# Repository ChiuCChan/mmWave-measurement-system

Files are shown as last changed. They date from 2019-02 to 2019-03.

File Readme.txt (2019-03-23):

=============Title=======================
Open-Source and Low-Cost Test Bed for Automated 5G Channel Measurement in mmWave Band

=============Movitation==================
To provide an affordable and open-source test-bed solution for mmWave channel modeling 
covering 24 GHz and 77 GHz bands. 

=============Built with Arduino==========

=============Specification==========
Carrier frequnecy	24GHz		77GHz
Signal bandwidth	15kHz		0.15MHz
Transmit power		20 +/- 1 dBm    25 +/- 2 dBm
Antenna Gain		20 dB		20 dB
H-plane beamwidth	80 deg		15 deg
E-plane beamwidth	12 deg		15 deg

=============Library used================
---24 Ghz module---
Wire.h Adafruit_MCP4725.h stdlib.h

---Base Unit---
<AccelStepper.h> <Adafruit_GFX.h> <Adafruit_SSD1306.h> <SPI.h> 
<RF24.h>(from github) <stdlib.h> <string.h> <TinyGPS++.h>

---Base Station---
<RF24.h> <SPI.h>

===========Electronics BoQ================
RS232+BT x2
Op Amp x2
Arduino nano x2
Arduino Duo x3
GY-4988 x2
nRF24L01 x2
Antenna x3 
OLED x2
ADC+DACx2
Doppler Radar RS3400 x2(77GHz)x2
Doppler Radar KLC-6 x2(24GHz) x2
GPS+RTL x2
Power regulator (YL105) x2
XY42STH34-1504A (High Stepper motor) x2

==================Pin setup================
---24 GHz module---
A0<->KLC6 Output

---Base Unit---
Serial 2 <-> GPS
Pin 50 <-> 4988 stepPin
Pin 51 <-> 4988 DirectionPin
Pin 46 <-> Optical switch Output
Pin 12 <-> OLED_CLK   
Pin 11 <-> OLED_MOSI  
Pin 10 <-> OLED_RESET 
Pin 09 <-> OLED_DC   
Pin 08 <-> OLED_CS   
Pin 13 <-> OLED_Power
Pin 52 <-> NF24L01 CEpin
Pin 53 <-> Nf24L01 CSpin

---Base Station---
Pin 52 <-> NF24L01 CEpin
Pin 53 <-> Nf24L01 CSpin

=============How to use?====================
comply different programs with respect to the corresponding unit.

For 77GHz radar measurement, RS232<->TTL modules are required for communication between Base Unit and 77GHz radar.
Or connect to the PC using RS232 and run the SiversIMA_Controller.m directly from the PC.
Run the BaseStation program and log into the Base Station CLI using arduino IDE or Putty

Using the following command to control the base unit, 77GHz, 24GHz radars.

//          Command                   Code             Respond
//          Force initialization      NNM01#          ”OK”
//          Reset angle               NNM02#          ”OK”
//          Get status                NNM03#           <text>
//          Get coordinates           NNM04#           S dd.dd / E ddd.dd
//          Get current angle         NNM05#            +/- ssss
//          relay                     NNM06<text>#      "Sent"
//          Go to angle               NNM10(+/-)ssss#   ”Go to +/- ssss”
//          Set 24GHz VCO voltage     NNM23VV#          "Set VCO to VV"
//	    Perform Sweeping from     NNM22VVVV#	Measurement data
	    VV to VV
//	    Troubleshooting	      NNM21#		Measurement data

The 77GHz radar command please refer to Sivers IMA RS3400 manual

==================Contribute==================
The Base Station and Base Unit program is programmed by Chiu Chan
The 24GHz radar controlling program is programmed by Ferdi Kurnia
The 77GHz radar controlling program is programmed by Akram Hourani

==================Credits==================
Thanks for the colleagues from RMIT University, AU for the hardware development and 3D printing 

==================License==================
Electronic & Telecommunication department, RMIT University, hereby disclaims all copyright interest in the program "mmWave measurement testbed" written by Chiu Chan, Ferdi Kurnia, Akram Hourani.

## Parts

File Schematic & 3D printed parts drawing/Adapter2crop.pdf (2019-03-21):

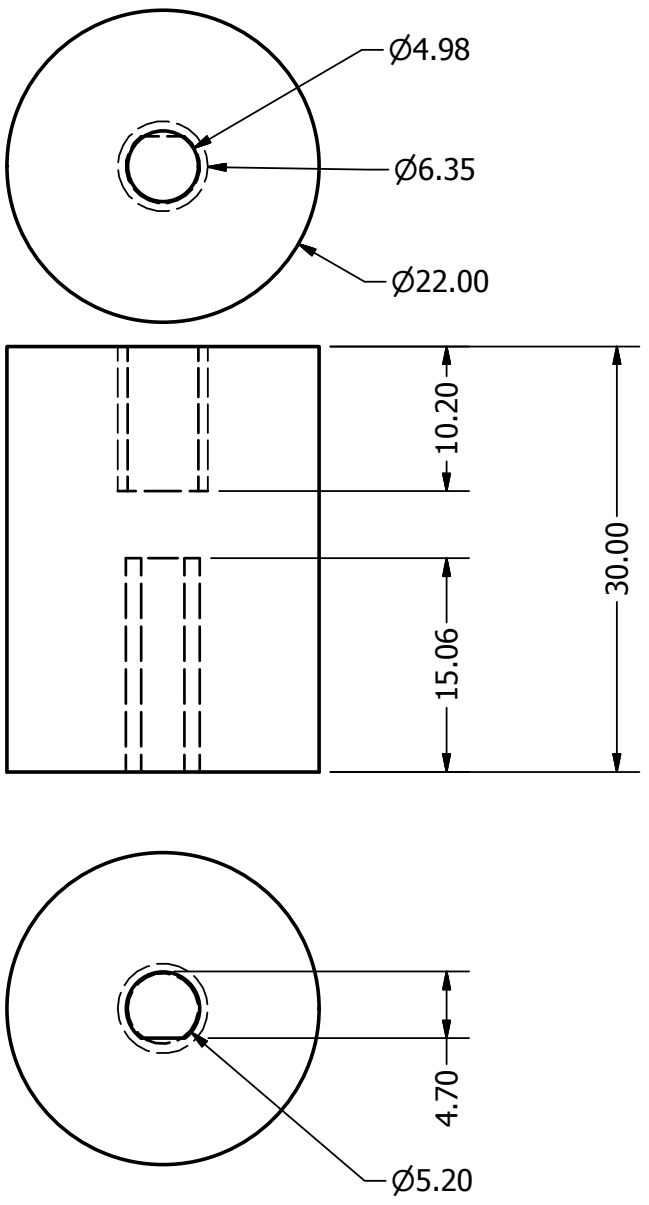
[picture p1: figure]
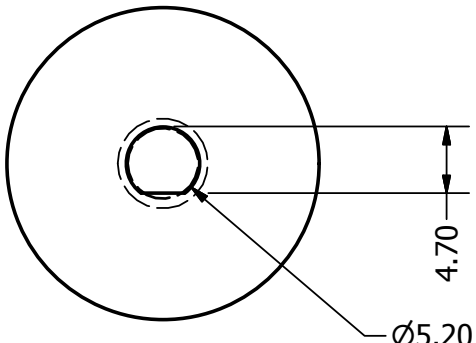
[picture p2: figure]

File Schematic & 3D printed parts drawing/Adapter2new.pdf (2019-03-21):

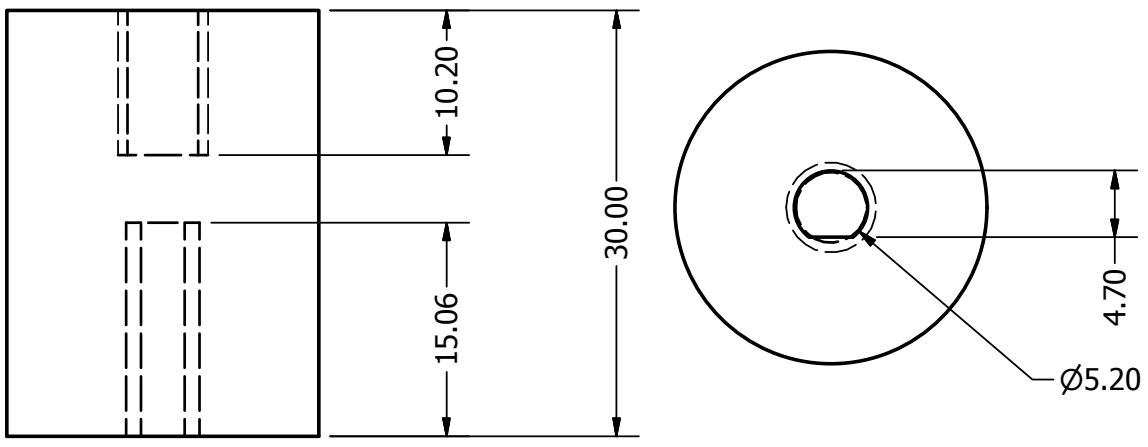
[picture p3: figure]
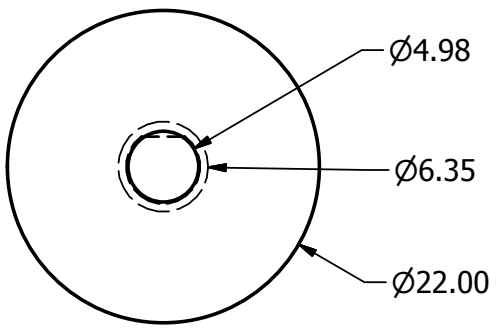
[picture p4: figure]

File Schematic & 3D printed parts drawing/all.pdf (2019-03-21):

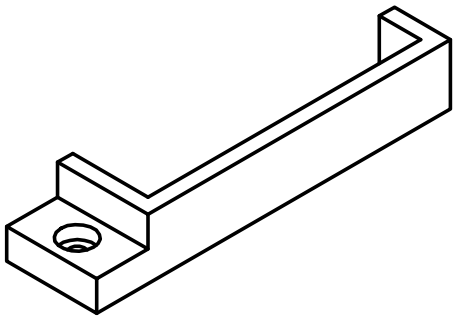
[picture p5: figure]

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
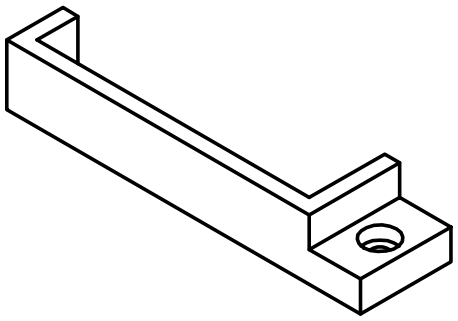
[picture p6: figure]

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
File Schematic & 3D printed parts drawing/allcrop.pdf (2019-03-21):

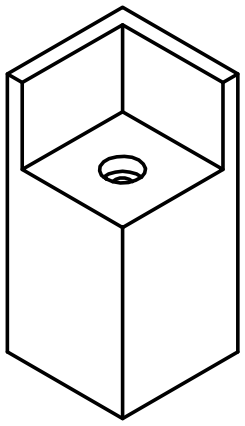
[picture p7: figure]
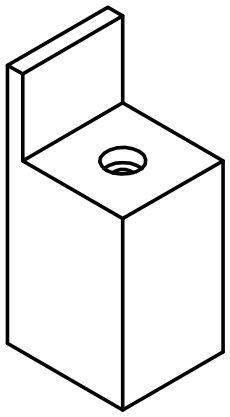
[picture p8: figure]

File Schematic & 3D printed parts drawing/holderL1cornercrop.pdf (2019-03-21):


3.00



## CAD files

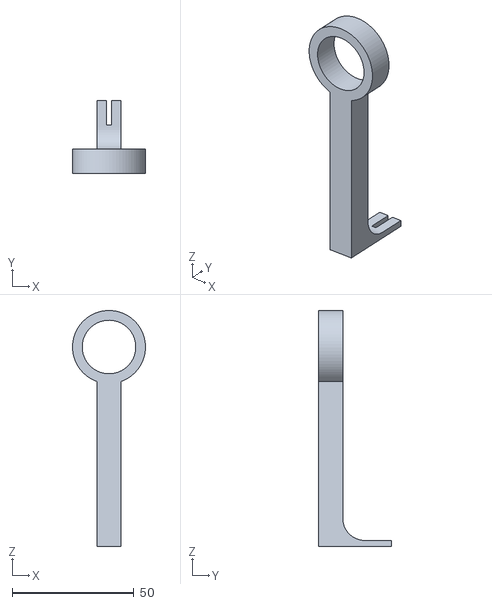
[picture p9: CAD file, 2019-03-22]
Schematic & 3D printed parts drawing/reseter-new-10.stl
30.0 x 30.0 x 97.0

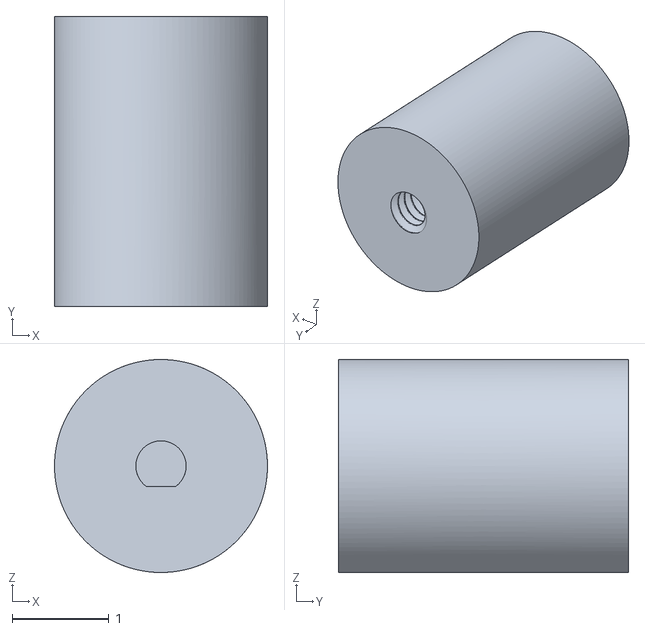
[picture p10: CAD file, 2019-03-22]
Schematic & 3D printed parts drawing/Adapter2-new.stl
2.20 x 3.00 x 2.20

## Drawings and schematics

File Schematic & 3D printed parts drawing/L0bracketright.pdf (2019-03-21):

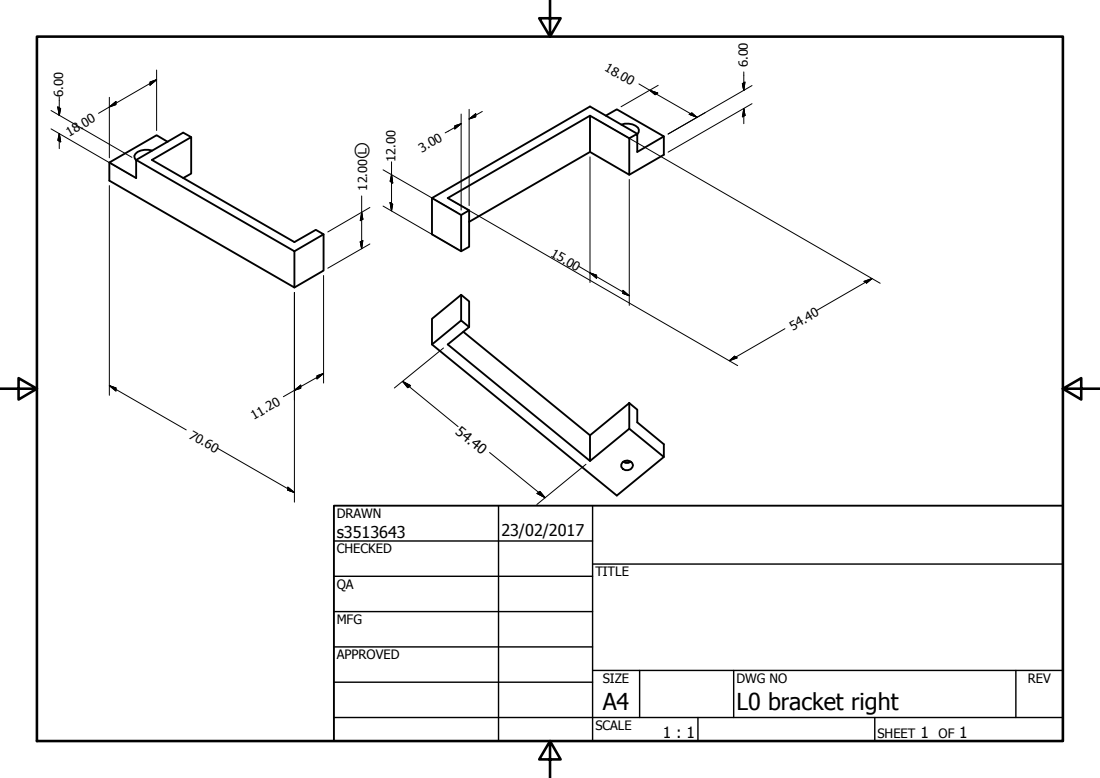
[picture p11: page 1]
SHEET 1 OF 1; DRAWN; CHECKED; MFG; APPROVED; DWG NO L0 bracket right; TITLE; SIZE A4; SCALE; REV

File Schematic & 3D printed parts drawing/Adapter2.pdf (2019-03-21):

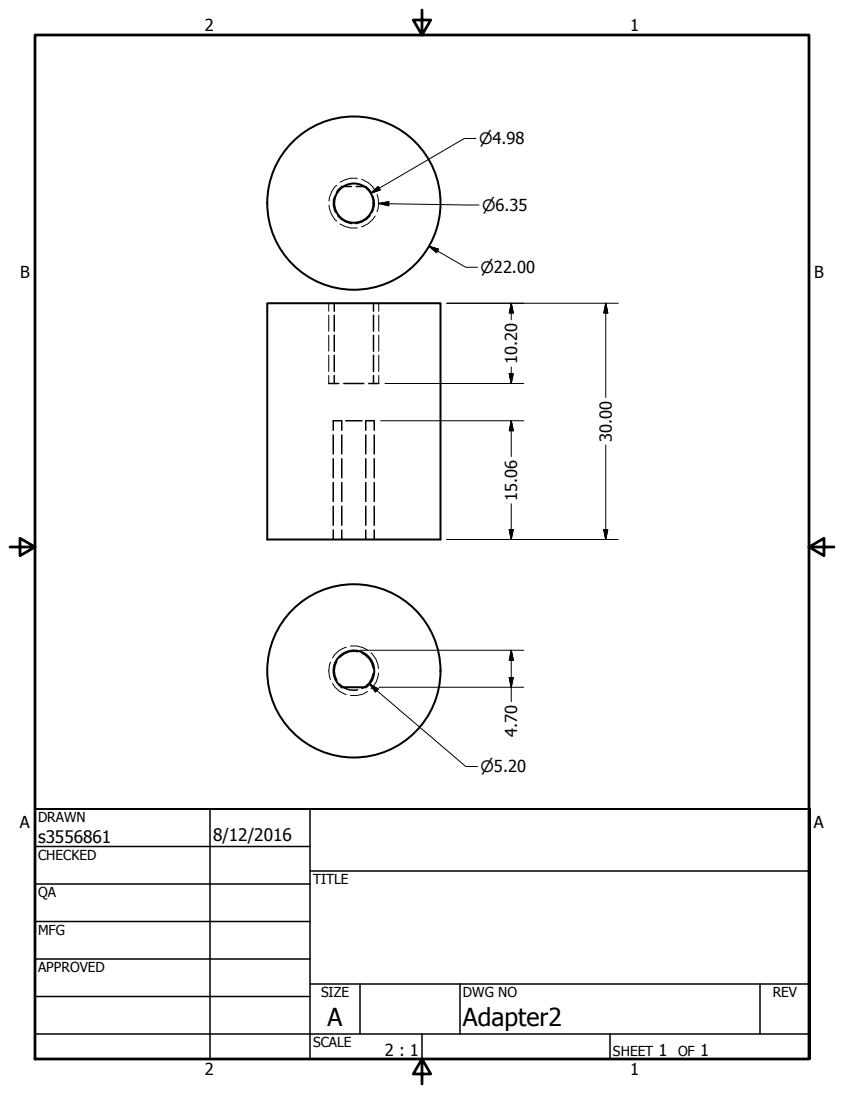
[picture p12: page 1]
SHEET 1 OF 1; DRAWN; CHECKED; MFG; APPROVED; DWG NO Adapter2; TITLE; SIZE A; SCALE; REV

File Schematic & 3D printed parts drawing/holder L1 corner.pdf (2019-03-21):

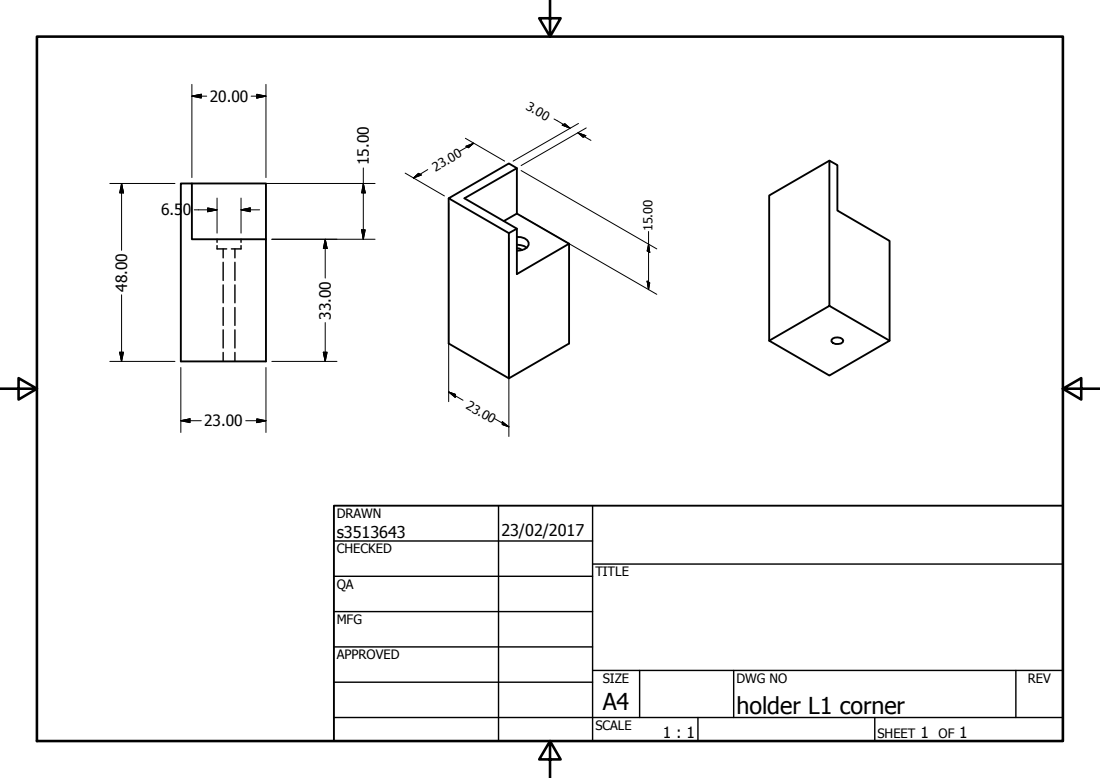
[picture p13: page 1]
SHEET 1 OF 1; DRAWN; CHECKED; MFG; APPROVED; DWG NO holder L1 corner; TITLE; SIZE A4; SCALE; REV

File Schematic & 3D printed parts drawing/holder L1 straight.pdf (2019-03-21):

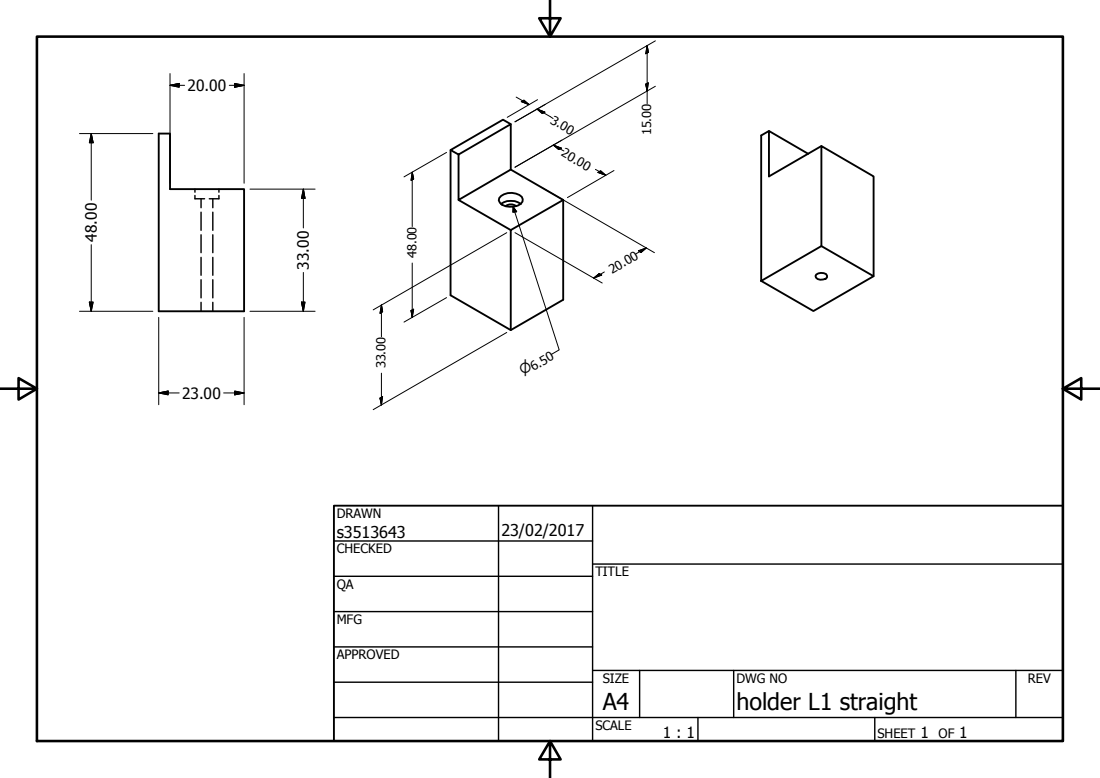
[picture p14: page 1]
SHEET 1 OF 1; DRAWN; CHECKED; MFG; APPROVED; DWG NO holder L1 straight; TITLE; SIZE A4; SCALE; REV

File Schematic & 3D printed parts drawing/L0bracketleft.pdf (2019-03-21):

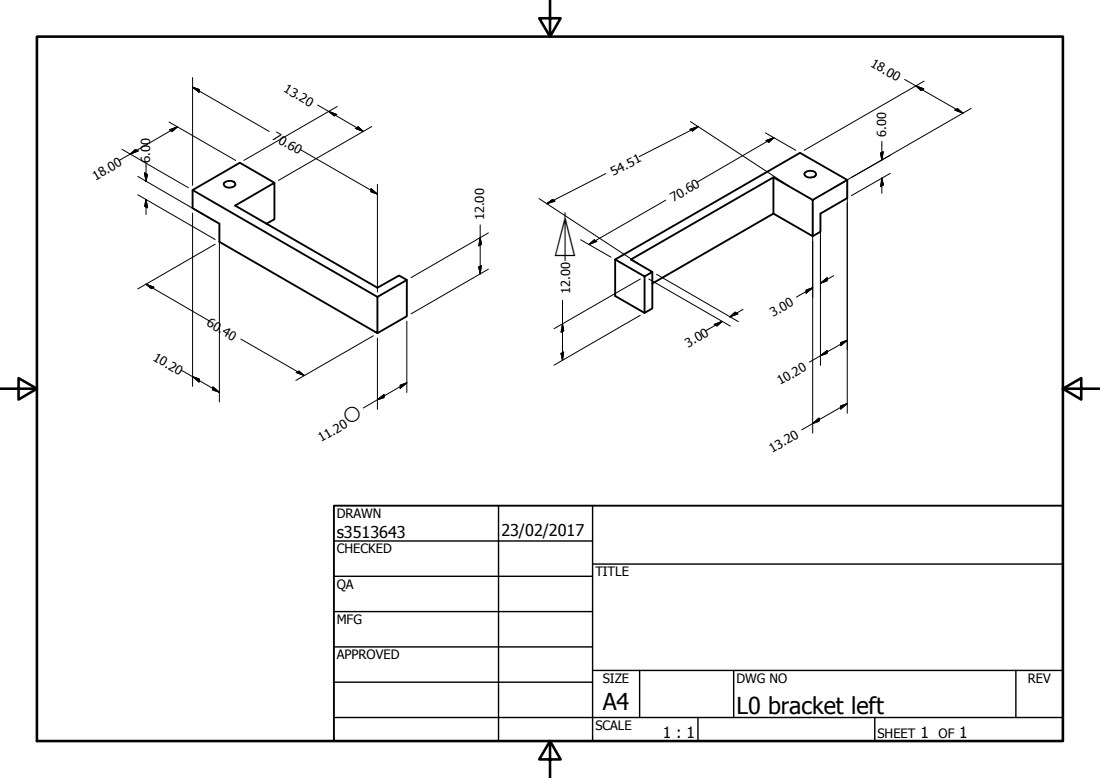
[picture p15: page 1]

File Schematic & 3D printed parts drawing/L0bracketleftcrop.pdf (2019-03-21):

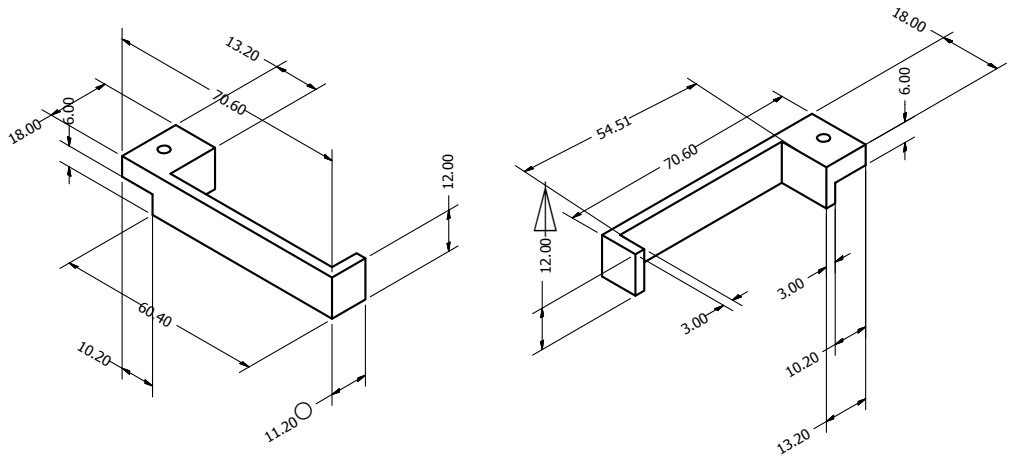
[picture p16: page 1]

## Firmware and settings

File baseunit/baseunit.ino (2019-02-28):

//
//float val = 0;          // variable to store the value read
//float Voltage;          // Analog voltage
//float Volt[10];         // Analog voltage array
//float averagevolt=0;    // average of the input voltage
//int displaycounter=0;
//#define analogPin 3     // potentiometer wiper (middle terminal) connected to analog pin 
                          // outside leads to ground and +5V


/**************************************************/
#include <AccelStepper.h>
#include <Adafruit_GFX.h>
#include <Adafruit_SSD1306.h>
#include <SPI.h>
#include "RF24.h"
#include <stdlib.h>
#include <string.h>
#include <TinyGPS++.h>
/**************************************************/
// The TinyGPS++ object
TinyGPSPlus gps;
#define ss Serial2
#define GPSBaud 9600    // GPS have to be 9600Hz 
/**************************************************/
//NEMA 17 motor pins
#define DRIVER 1
#define stepPin 50
#define dirPin 51       // initialize the stepper library on pins 50 51: 51=step 50=direction
AccelStepper myStepper(DRIVER,stepPin, dirPin);
/**************************************************/
//Optical Switch pin
#define opticalsw 46
/**************************************************/
// OLED screen pins
#define OLED_CLK   12
#define OLED_MOSI  11
#define OLED_RESET 10
#define OLED_DC    9
#define OLED_CS    8
#define OLED_Power 13
#define Buzzer 3
Adafruit_SSD1306 display(OLED_MOSI, OLED_CLK, OLED_DC, OLED_RESET, OLED_CS);
/**************************************************/
//Radio pin
#define CEpin 52
#define CSpin 53

/***********************************************************/
/***      Set this radio as radio number 0 or 1         ***/
char radiodisplay[32];
int radioNumber = 1; // 0, 1for arduino RX; 2 for MATLAB RECEIVER
byte incomingByte;     // When byte is received from the Radio
short int Buffer_index = 0;
char inData[52];       //Serial data buffer
char Command[52];      //The command received from serial port
double latdeg = 0;     //GPS latitude degree
double longdeg = 0;    //GPS longitude degree
bool error = 0;       //for checking command error
double angle=0;       //used to record current angle
String serialbuffer;
char charbuffer[1000];
char buffershort[32];
/* Hardware configuration: Set up nRF24L01 radio on SPI bus plus pins 7 & 8 */
RF24 radio(CEpin, CSpin); // (uint8_t _cepin, uint8_t _cspin)
/**********************************************************/
//byte addresses[3][6] = {"1Node", "2Node","3Node"};

byte Node1[2][7] = {"1Node", "2Node"};
byte Node2[2][7] = {"3Node", "4Node"};

// Used to control whether this node is sending or receiving

// Our function
void beep(unsigned char delayms) 
 { //creating function
  digitalWrite(Buzzer, LOW); //Setting pin to low
  delay(delayms); //Delaying
  digitalWrite(Buzzer ,HIGH); //Setting pin to high
  delay(delayms); //Delaying;r
 }
 
void moveto()
{
 char Stepc[4];
 int Stepint = 0;

 memset(Stepc,0,sizeof(Stepc));
              for (int i = 0 ; i < 4; i++) 
              {
                Stepc[i] = Command[i + 7]; //copy  digits 7,8,9,10 step
              }
              if (strstr(Command,"+"))
              {
              //  display.println("debug1");
                Stepint=atoi(Stepc);
              }
              else if (strstr(Command,"-"))
              {
                //display.println("debug2");
                Stepint= -atoi(Stepc);
              }
              display.print("Move to position");
              display.println(Stepint); 
              Serial.println(Stepc);
              display.display();
              radio.write("N2 moved to position:",21);
              radio.write(Stepc,sizeof(Stepc));
              radio.write("\r",2);
              myStepper.setCurrentPosition(0);      
              myStepper.runToNewPosition(Stepint); // Move steps (1.8 degree for one step)
              angle+=(Stepint*1.8)/16;
              angle=angle/360;
         
              delay(2000);
}

void getstatus(double currentangle)
{
  radio.write("Current Angle:\r",15);
  memset(radiodisplay,0,32);
  snprintf(radiodisplay,32,"%f",currentangle);
  radio.write(&radiodisplay, sizeof(radiodisplay));
  radio.write("\r",2);
}
void relay()
{
  char msg32[32];
  memset(msg32,0,sizeof(msg32));
  for(int i=0; Command[i + 6] != '#' ;i++)
  {
    msg32[i] = Command[i + 6]; //copy  digits 6,8,9,10 step
  }
  
  serialbuffer =String(msg32);
  
  Serial1.print(serialbuffer + "\r");
  Serial.println(serialbuffer);        //for debug
  display.println(serialbuffer);
  display.display();
  delay(100);
}


void relay22()
{
  char msg32[32];
  memset(msg32,0,sizeof(msg32));
  int i=0;
  for(i=0; Command[i + 6] != '#' ;i++)
  {
    msg32[i] = Command[i + 6]; //copy  digits 6,8,9,10 step
  }
  msg32[i] = '#';
  serialbuffer =String(msg32);
  
  Serial3.print(serialbuffer);
  Serial.println(serialbuffer);        //for debug
  display.println(serialbuffer);
  display.display();
  //delay(100);
}

void calibrate()
{
  radio.write("Start Calibrate\r",17);
  for(int i=0;i<360;i++)
  {
      myStepper.setCurrentPosition(0);      
      myStepper.runToNewPosition(8.888); // Move one step (1.8 degree for one step)
      if (digitalRead(opticalsw) == LOW)       //Try to get "01" signal to calibrate
      {
          myStepper.setCurrentPosition(0);      
          myStepper.runToNewPosition(8.888); // Move one step (1.8 degree for one step)
          if (digitalRead(opticalsw) == HIGH)
          {
              myStepper.setCurrentPosition(0);
              myStepper.runToNewPosition(8.888); // Move one step (1.8 degree for one step)
              radio.write("OK\r",4);
              display.println("Finish Calibration!");
              display.display();
              return;
          }   
      }
  }
}

void GPSget(double latitude,double longitude)     //GPS function for getting lattude & longitude
{
  latitude = gps.location.lat();
  delay(100);
  longitude = gps.location.lng();
  delay(100);
  radio.write("S:",2);
  delay(100);
  snprintf(radiodisplay,50,"%f",latitude);
  radio.write(&radiodisplay,sizeof(latitude));
  delay(100);
  radio.write("E:",2);
  delay(100);
  memset(radiodisplay, 0, 32);
  snprintf(radiodisplay,50,"%f",longitude);
  radio.write(&radiodisplay,sizeof(longitude));
  delay(100);
  radio.write("\r",sizeof("\r"));
  if (millis() > 5000 && gps.charsProcessed() < 10)
  {
    Serial.println(F("No GPS data received: check wiring"));  //for debugging
    display.clearDisplay();  ///LED module
    display.setCursor(0, 0);
    display.println("No GPS data received");
    display.print("Lat:");
    display.println(latitude);
    display.print("Long:");
    display.println(longitude);
    display.display();      ///LED module
  }
  else
  {
    display.clearDisplay();  ///LED module
    display.setCursor(0, 0);
    display.print("Lat:");
    display.println(latitude);
    display.print("Long:");
    display.println(longitude);
    display.display();      ///LED module
  }
}

void setup()
{
  pinMode(opticalsw, INPUT);     //  Digital input from 
  pinMode(Buzzer, OUTPUT); //Set buzzerPin as output
  digitalWrite(Buzzer ,HIGH); //Setting pin to high
  
  // This is power up the OLED from the output pin
  pinMode(OLED_Power, OUTPUT);
  digitalWrite(OLED_Power, HIGH);
  
  //initialise stepper motor
  myStepper.setMaxSpeed(500.0);
  myStepper.setAcceleration(5000.0);
  myStepper.setSpeed(500);

   // Initilize GPS
  ss.begin(GPSBaud);
  // Initilize Relay module
  Serial1.begin(115200);
  Serial3.begin(115200);
  // Initilize OLED
  display.begin(SSD1306_SWITCHCAPVCC);
  display.clearDisplay();
  display.setTextSize(1);
  display.setTextColor(WHITE);
  display.setCursor(0, 0);
  display.println("mmWave demoV6");
  display.println("akram.hourani");
  display.println("@rmit.edu.au");
  display.println("20170504");
  display.display();
  delay(500);
 
  //  setup serial
  Serial.begin(115200);
  Serial.println("mmWave motherbroad");
  Serial.println("akram.hourani@rmit.edu.au");
  Serial.println("");
  Serial.println("Radio Properties:");
  radio.begin();

  // Set the PA Level low to prevent power supply related issues since this is a
  // getting_started sketch, and the likelihood of close proximity of the devices. RF24_PA_MAX is default.
  radio.setPALevel(RF24_PA_MAX);
  radio.setDataRate(RF24_2MBPS);
  radio.printDetails();
  radio.setChannel(125);

  // Set the pipe addressess ** make sure you have the opposite addresses on the SLAM Car
  if (radioNumber==2)  //open pipe for communication
  {
    radio.openReadingPipe(1,Node2[0]);
    radio.openWritingPipe(Node2[1]);
    radio.stopListening();
    radio.setChannel(75);
    radio.write("Node2 online",13);
  }
  else if(radioNumber==1)
  {
    radio.openReadingPipe(1,Node1[0]);
    radio.openWritingPipe(Node1[1]);
    radio.stopListening();
    radio.setChannel(125);
    radio.write("Node1 online",13);
  }
  Serial.println("");
  Serial.println("Trasmitter ready... ok");
}

void loop()
{
  radio.startListening(); //RX Mode
  display.clearDisplay();
  display.setCursor(0,0);
  display.println("Listening to Radio");
  display.display();
  if (radio.available()) 
  {
      radio.read( &incomingByte, sizeof(incomingByte) );
      inData[Buffer_index] = incomingByte;
      Buffer_index++;
      radio.stopListening();
      
      //When a commdan is ready execute the following
      if (inData[Buffer_index - 2] == '#' && Buffer_index > 1)  
      {
        memset(Command, 0, sizeof(Command)); // Clear recieved buffer
        strncpy(Command, inData, Buffer_index); // Save the command
        memset(inData, 0,sizeof(inData));
        Serial.print(inData);  
       
        Buffer_index = 0; // reset the buffer pointer
 
        display.clearDisplay();  ///LED module /for debugging
        display.setCursor(0, 0);
        display.print("Command: ");
        display.println(Command);
        display.display();      ///LED module

//          Command                   Code             Respond
//          Force initialization      NNM01#          ”OK”
//          Reset angle               NNM02#          ”OK”
//          Get status                NNM03#           <text>
//          Get coordinates           NNM04#           S dd.dd / E ddd.dd
//          Get current angle         NNM05#            +/- ssss
//          relay                     NNM06<text>#      "Sent"
//          Go to angle               NNM10(+/-)ssss#   ”Go to +/- ssss”
        
            if(strstr(Command,"N1M01") || strstr(Command,"N2M01"))
            {
//              initialization();
            }
            else if(strstr(Command,"N1M02") || strstr(Command,"N2M02") )
            {
              calibrate();
              angle=0;
            }
            else if(strstr(Command,"N1M03") || strstr(Command,"N2M03"))
            {
              getstatus(angle);
            }
            else if(strstr(Command,"N1M04") || strstr(Command,"N2M04"))
            {
              GPSget(latdeg,longdeg); 
            }
            else if(strstr(Command,"N1M06") || strstr(Command,"N2M06"))
            {
              relay();
            }
            else if(strstr(Command,"N1M07") || strstr(Command,"N2M07"))
            {
              relay22();
            }
            else if(strstr(Command,"N1M10") || strstr(Command,"N2M10"))
            {
              moveto();  
            }
      }
  }
  while(Serial1.available())
  {
    radio.stopListening();
    memset(buffershort,'\0',sizeof(buffershort));
    serialbuffer = Serial1.readBytes(buffershort,30); // reading 32 bytes  
    Serial.println(buffershort);
    radio.write(buffershort,30);
  }
  while(Serial3.available())
  {
    radio.stopListening();
    memset(buffershort,'\0',sizeof(buffershort));
    Serial3.readBytes(buffershort,32); // reading 32 bytes  
    Serial.print(buffershort);
    radio.write(buffershort,32);
  }
  
  
  //delay(20);

}

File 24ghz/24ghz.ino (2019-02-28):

#include <Wire.h>
#include <Adafruit_MCP4725.h>
#include <stdlib.h>

#define voltsIn A0

Adafruit_MCP4725 dac; // constructor

/////////////////////////////////////////////////////////////
char inData[52]; //Serial data buffer
short int Buffer_index = 0;
char Command[52];      //The command received from serial port
byte incomingByte;
char conc_val[52];

#define n_sample_1 100
float volt_array_1[n_sample_1];
float E = 0.0;
float  volt_avg, volt_max_temp;

int delay_val = 1;//delay between sample
int delay_voltage = 100;//delay between Setting up VCO voltage to taking first ADC value
    
/////////////////////////////////////////////////////////////

int x = 0;
String inputread, endchar;
char val; // Data received from the serial port

int getIndexOfMaximumValue(float* array, int size)
{
  int maxIndex = 0;
  float max = array[maxIndex];
  for (int i=0; i<size; i++)
  {
    if (max < array[i])
    {
      max = array[i];
      maxIndex = i;
    }
  }
  return maxIndex;
}

void setup(void) 
{
  Serial.begin(115200);
  dac.begin(0x60); // The I2C Address: Run the I2C Scanner if you're not sure      
  Serial.println("24 GHz Front-End");
}

void start_measuring()
{
    int adcValueRead = 0;
    float voltageRead = 0;
       
    inputread = "";
    
    for(int i = 0 ; i < 100 ; i++)
    {
        adcValueRead = analogRead(voltsIn);
        voltageRead = (adcValueRead * 5.0)/ 1024.0;
           
           if(i == 99)
            {
              endchar =  '#';
              inputread = inputread + voltageRead + endchar;
            } 
            
            if (i > 0 && i < 99)
            {
              endchar =  ", ";
              inputread = inputread + voltageRead + endchar;
            } 
            
            if (i == 0)
            {
              endchar =  ", ";
              inputread = voltageRead + endchar;
            }
            //inputread = inputread + voltageRead + endchar;
     
      }
    
      Serial.print(inputread);
      Serial.println();
}


void set_dac_voltage(char* dac_volt)
{
    uint32_t dac_value;
    float dac_expected_output;
      
    String inString1 = "";
    String inString2 = "";
    String inString3 = "";
    double val_volt, val_volt2, val_volt3;
    int v1, v2, v3;

    inString1 = Command[4];
    inString2 = Command[5];
    inString3 = Command[6];
    v1 = inString1.toInt();
    v2 = inString2.toInt();
    v3 = inString3.toInt();
              
    val_volt = (v1 * 100.0 + v2 * 10.0 + v3);
    val_volt2 = val_volt/100.0;
    Serial.println(v1);
    Serial.println(v2);
    Serial.println(v3);
    Serial.println(val_volt2);
    
    dac_value = ((val_volt2/2.0)/5.0*4096.0);//this is for single voltage value assignment
    
    dac_expected_output = ((val_volt2*2.0)/4096.0) * dac_value;
    dac.setVoltage(dac_value, false);
   
    Serial.println("Set DAC Voltage Success");
    
}

//void start_sweeping(char* Command)
void start_sweeping()
{
    uint32_t dac_value, dac_value1 = 0, dac_value2 = 0, dac_value_set;
    int adcValueRead = 0;
    float voltageRead = 0;
    float dac_expected_output, dac_start, dac_stop, volt_1;
    int val_s = 0, a = 0, N, pwmVolt, maxIndex, maxIndex_final, val_max[52];//204 to 255, variable to store the read value
    float volt_max_temp, max_array[52], dacv_array[52], dacv1_array[52]; 
    float sum = 0;
    
//    int n_sample = 50;
//    float volt_array[n_sample];
//    int val_array[n_sample];//0 to 1023

//    String inString1 = "";
//    String inString2 = "";
//    String inString3 = "";
//    String inString4 = "";
//    
//    double val_volt, val_volt2, val_volt3, val_volt4;
//    int v1, v2, v3, v4;
//
//    inString1 = Command[3];
//    inString2 = Command[4];
//    inString3 = Command[5];
//    inString4 = Command[6];
//    v1 = inString1.toInt();
//    v2 = inString2.toInt();
//    v3 = inString3.toInt();
//    v4 = inString4.toInt();
//              
//    val_volt = (v1 * 10.0 + v2);
//    val_volt2 = val_volt/10.0;
//    Serial.println(v1);
//    Serial.println(v2);
//    Serial.println(val_volt2);
//
//    val_volt3 = (v3 * 10.0 + v4);
//    val_volt4 = val_volt3/10.0;
//    Serial.println(v3);
//    Serial.println(v4);
//    Serial.println(val_volt4);
    
    //Calibrated Values
    //7.5 (DAC value) ==> 7.61 (DCV read)
    //7.4 ==> 7.48
    //7.35 ==> 7.44
    //7.3 ==> 7.39
    //7.25 ==> 7.33
    //7.2 ==> 7.28
    //7.1 ==> 7.19 

    //dac_start = val_volt2;//7.4
    //dac_stop = val_volt4;//7.6

    dac_start = 7.2;
    dac_stop = 7.5;
    
    dac_value1 = ((dac_start/2.0)/5.0*4096.0);//2990 (7.3)
    dac_value2 = ((dac_stop/2.0)/5.0*4096.0);//3112 (7.6)

    Serial.print("Start Sweeping from ");
    Serial.print(dac_start);
    Serial.print(" V to ");
    Serial.print(dac_stop);
    Serial.print(" V");

    N = (dac_value2 - dac_value1)/5;
    
    for (dac_value = dac_value1; dac_value < dac_value2; dac_value = dac_value + 5) //this is for voltage sweeping
    {
      sum = 0;
      E = 0.0;

      //1 Set the DAC Value
      dac.setVoltage(dac_value, false);
      
      delay(delay_voltage);//delay between the voltage
      
      //2 Capture received voltage
      
      for(int i = 0 ; i < n_sample_1 ; i++) 
      { 
        val_s             = analogRead(voltsIn); //read the voltage from A0
        volt_1            = val_s*5.0;
        volt_array_1[i]   = volt_1/1023.0;
        
        delay(delay_val);//delay is between the sample
        
//        Serial.println(" ");
//        int j = i + 1;
//        Serial.print(j);    
//        Serial.print("\t");
//        Serial.print(volt_array_1[i] ,6);
        sum += volt_array_1[i] ;
      }//close bracket for
       
      //3 Get average voltage
      volt_avg = sum/n_sample_1;
     dac_expected_output = ((5.0*2.0)/4096.0) * dac_value;
//      Serial.println(" ");
//      Serial.print("Average[");
//      Serial.print(dac_expected_output);
//      Serial.print("] = ");
//      Serial.print(volt_avg,6);
     
      //4 Calculate energy
      for(int i = 0 ; i < n_sample_1 ; i++) 
      { 
        float temp;
        temp = volt_array_1[i];
        volt_array_1[i] = (temp - volt_avg)*1000.0;
//        Serial.println(" ");
//        Serial.print("Minus avg : ");
//        Serial.print(volt_array_1[i],6);
//        Serial.print(" mV");

        temp = 0;
        temp = volt_array_1[i] * volt_array_1[i];
        E = E + temp;
//        Serial.println(" ");
//        Serial.print("Squared : ");
//        Serial.print(temp,6);
        
      }//close bracket for
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
